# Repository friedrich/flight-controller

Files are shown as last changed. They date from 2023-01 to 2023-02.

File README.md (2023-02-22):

# Flight controller

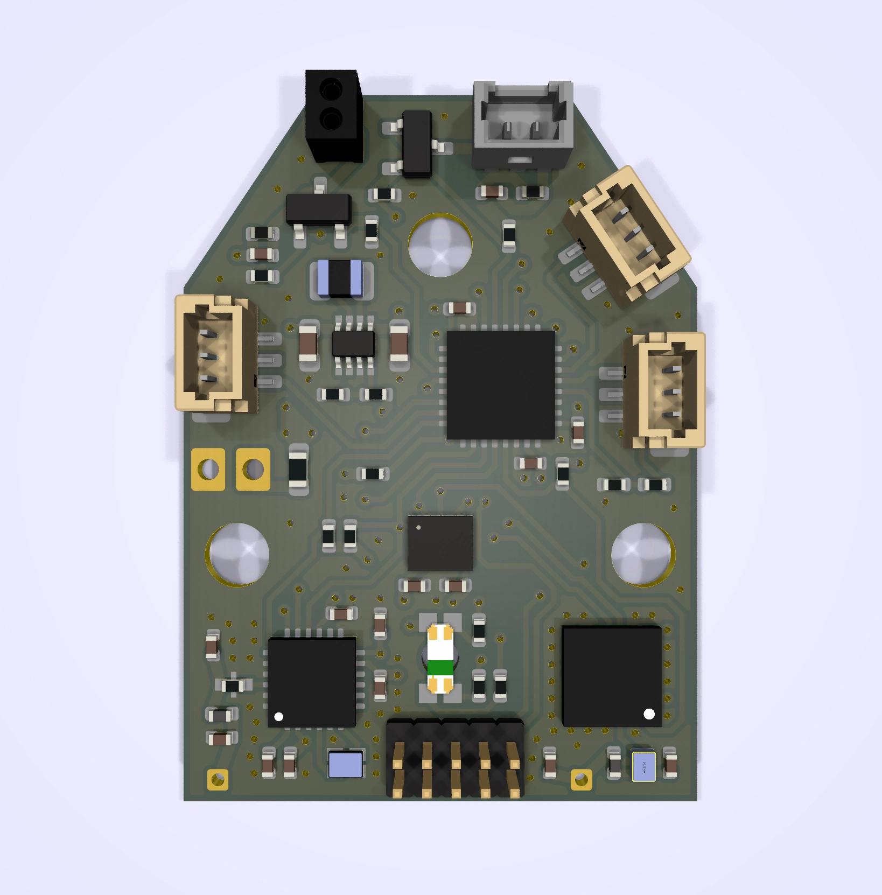
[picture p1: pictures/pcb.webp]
rendering

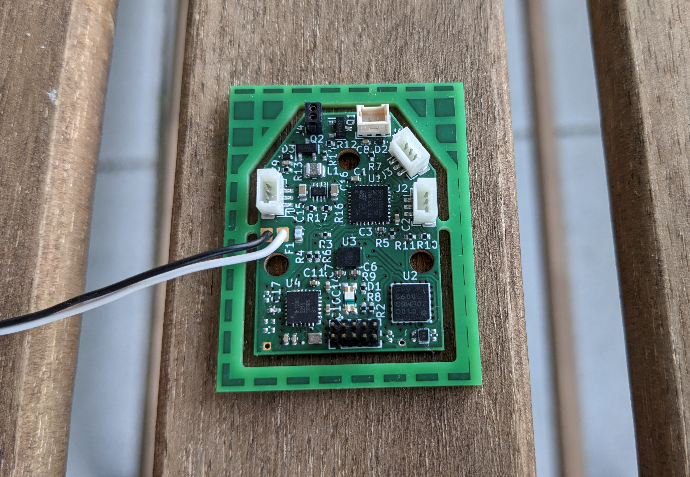
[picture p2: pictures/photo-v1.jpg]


# Hardware features

- :heavy_check_mark: Voltage regulator delivering 3.3 V to the ICs
- :x: Battery voltage monitor
  - Battery voltage monitor pin PA10 is not connected to a DAC.
- :heavy_check_mark: Pulse width modulated power supply of the main and tail rotor motors
- :x: Current monitor of the main and tail rotor motors
  - Pins PF0 and PF1 are not connected to any operational amplifiers. This makes
    current sensing inaccurate, since the shunt voltage is quite low.
- :heavy_check_mark: PWM control of the swashplate servos
- :heavy_check_mark: Programming and debugging interface via SWD and SWO
- :heavy_check_mark: Linear acceleration sensor and gyroscope
- :x: GPS receiver
  - No usable signal from antenna.
  - There is no good return path for the antenna signal.
- :x: Radio module with support for BLE, LoRa, FLRC, GFSK and ranging
  - Untested.
  - There is no good return path for the antenna signal.
- :heavy_check_mark: RGB status indicator LED
- :heavy_check_mark: Overcurrent protection (fuse)

## Possible improvements

- Connect reset pins of other ICs to the microcontroller.
- Connect the SX1280 busy pin and multi-purpose digital I/O pins to the
  microcontroller.
- Connect one PIO pin of the GNSS receiver to the microcontroller for TX ready
  notification.
- Add test points to GND, CS, SDI, SDO, SCK, RESET.
- Print version number on the PCB.
- Remove silk screen labels of small compenents.
- Make it possible to manually pull up the BOOT0 pin in case the firmware
  disrupts SWD communication.
- The top internal layer should be a ground plane to ensure a nice return path
  for the RF signal. Make a six layer board with layers: signal, ground, signal,
  power, signal, ground.

# GPIO pins

| Pin  | Function | Configuration |
|---|---|---|
| PA0  | | |
| PA1  | TAIL_CTL | TIM15_CH1N |
| PA2  | LEFT_CTL | TIM2_CH3 |
| PA3  | /RADIO_CS  | output |
| PA4  | /ACCEL_CS  | output |
| PA5  | SCK | SPI1_SCK |
| PA6  | SDI | SPI1_MISO |
| PA7  | SDO | SPI1_MOSI |
| PA8  | | |
| PA9  | | |
| PA10 | BATT_MON | |
| PA11 | RIGHT_CTL  | TIM4_CH1 |
| PA12 | BACK_CTL | TIM4_CH2 |
| PA13 | SWDIO | SWDIO |
| PA14 | SWCLK | SWCLK |
| PA15 | | |
| PB0  | /GNSS_CS | output |
| PB3  | SWO | TRACESWO |
| PB4  | LED_R | TIM3_CH1 |
| PB5  | LED_G | TIM3_CH2 |
| PB6  | MAIN_CTL | TIM16_CH1N |
| PB7  | LED_B | TIM3_CH4 |
| PF0  | MAIN_SENSE | ADC1_IN10 |
| PF1  | TAIL_SENSE | ADC2_IN10 |

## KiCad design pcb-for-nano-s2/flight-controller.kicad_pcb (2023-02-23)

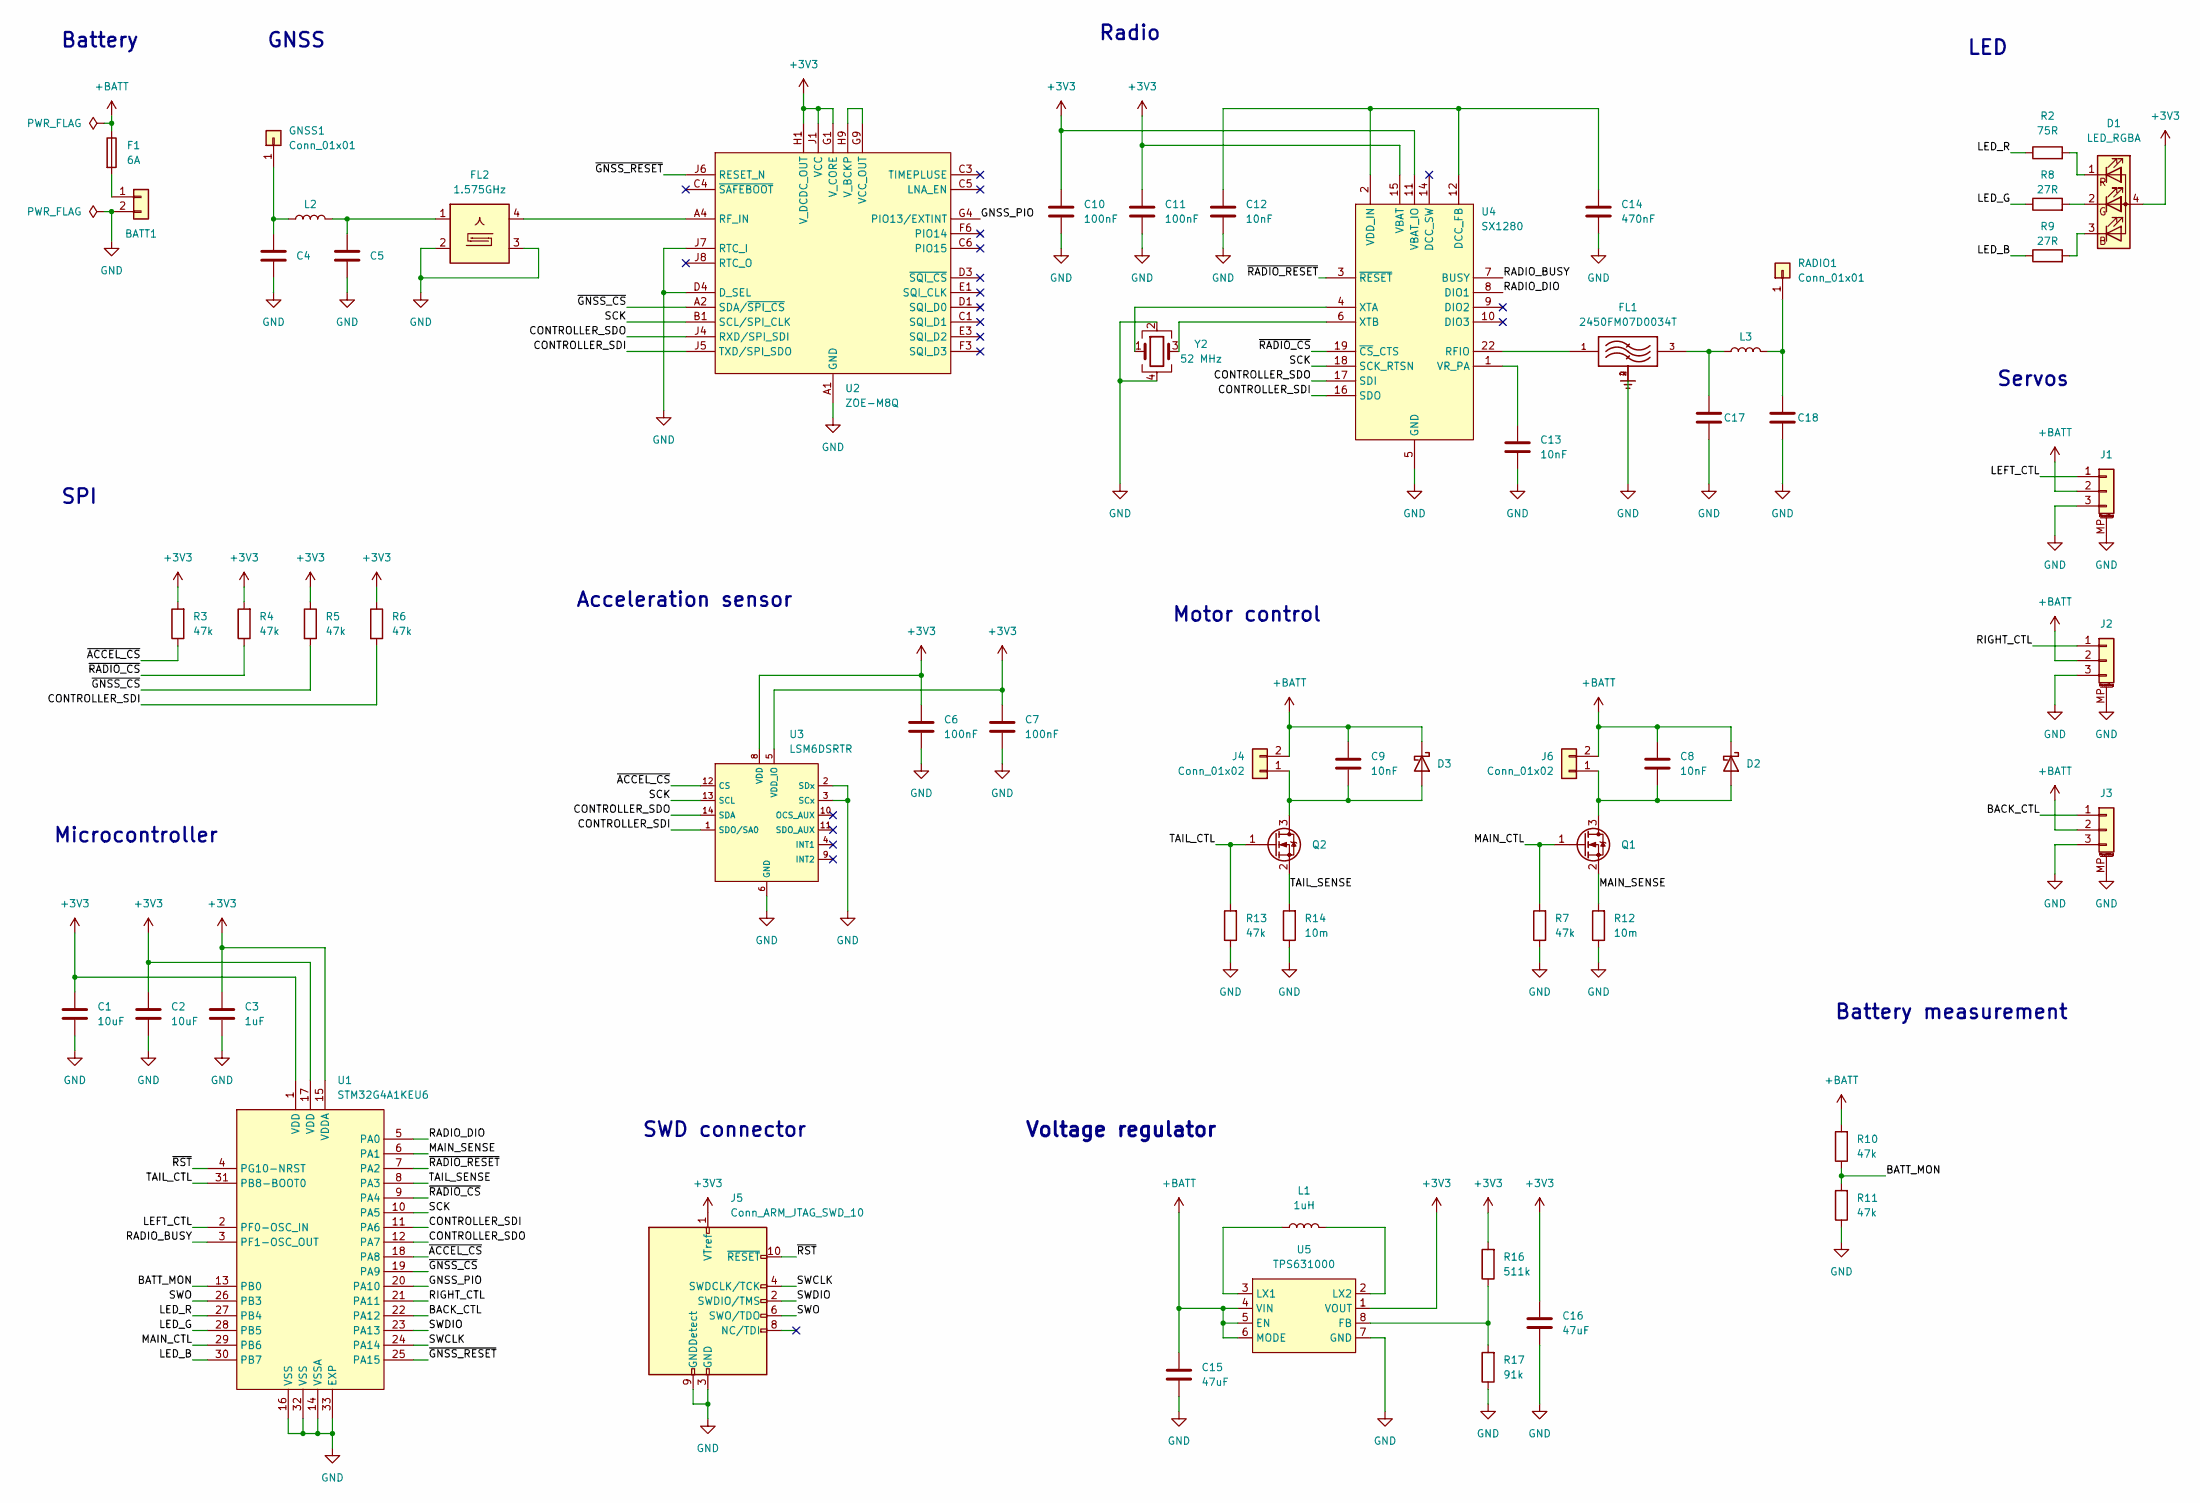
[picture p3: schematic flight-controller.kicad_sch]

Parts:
BATT1: Conn_01x02; Conn
C1, C2: 10uF; C_0402_1005Metric; MPN GRM155R60J106ME15D
C3: 1uF; C_0402_1005Metric; MPN CL05A105MQ5NNNC
C4, C5, C17, C18: C_0402_1005Metric
C6, C7, C10, C11: 100nF; C_0402_1005Metric; MPN CL05A104KA5NNNC
C8, C9, C12, C13: 10nF; C_0402_1005Metric; MPN CL05B103KB5NNNC
C14: 470nF; C_0402_1005Metric; MPN CL05A474KP5NNNC
C15, C16: 47uF; C_0603_1608Metric; MPN GRM188R60J476ME15D
D1: LED_RGBA; LED_156125M173000; MPN 156125M173000
D2, D3: D_Schottky; D_0402_1005Metric; MPN RB521S-30L2-TP
F1: 6A; Fuse_0603_1608Metric; MPN 0686F6000-01
FL1: 2450FM07D0034T; FIL_2450FM07D0034T; MPN 2450FM07D0034T
FL2: 1.575GHz; Filter_1411-5_1.4x1.1mm; MPN AFS14A04-1575.42-T3
GNSS1: Conn_01x01; Antenna
J1, J2, J3: BM03B-SRSS-TBLFSN; JST_SH_BM03B-SRSS-TB_1x03-1MP_P1.00mm_Vertical; MPN CI1103M1VR0-NH
J4: Conn_01x02; PinHeader_1x02_P1.27mm_Vertical; MPN 851-87-002-10-001101
J5: Conn_ARM_JTAG_SWD_10; PinHeader_2x05_P1.27mm_Vertical; MPN GRPB052VWVN-RC
J6: Conn_01x02; Molex_PicoBlade_53047-0210_1x02_P1.25mm_Vertical; MPN 0530470210
L1: 1uH; 0806; MPN DFE201612E-1R0M=P2
L2, L3: L_0402_1005Metric
Q1, Q2: Q_NMOS_GSD; SOT-23; MPN IRLML6244TRPBF
R2: 75R; R_0402_1005Metric; MPN RC0402JR-0775RL
R3, R4, R5, R6, R7, R10, R11, R13: 47k; R_0402_1005Metric; MPN RC0402JR-0747KL
R8, R9: 27R; R_0402_1005Metric; MPN RC0402JR-0727RL
R12, R14: 10m; R_0402_1005Metric; MPN ERJ-2LWFR010X
R16: 511k; R_0402_1005Metric; MPN RC0402FR-07511KL
R17: 91k; R_0402_1005Metric; MPN RC0402FR-0791KL
RADIO1: Conn_01x01; Antenna
U1: STM32G4A1KEU6; UFQFPN-32-1EP_5x5mm_P0.5mm_EP3.5x3.5mm; MPN STM32G4A1KEU6
U2: ZOE-M8Q; componentsearchengine-BGA51C50P9X9_450X450X110; MPN ZOE-M8Q-0
U3: LSM6DSRTR; LGA-14_3x2.5mm; MPN LSM6DSRTR
U4: SX1280; HVQFN-24-1EP_4x4mm_P0.5mm_EP2.6x2.6mm; MPN SX1280IMLTRT
U5: TPS631000; SC-70-8; MPN TPS631000DRLR
Y2: 52 MHz; XTAL_ECS-520-8-47-CKM-TR; MPN ECS-520-8-47-CKM-TR

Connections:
+3V3: C1.1, C2.1, C3.1, C6.1, C7.1, C10.1, C11.1, C16.1, D1.4 (A), J5.1 (VTref), R3.2, R4.2, R5.1, R6.1, R16.2, U1.1 (VDD), U1.15 (VDDA), U1.17 (VDD), U2.G1 (V_CORE), U2.H1 (V_DCDC_OUT), U2.J1 (VCC), U2.J2 (VCC), U3.5 (VDD_IO), U3.8 (VDD), U4.11 (VBAT_IO), U4.15 (VBAT), U5.1 (VOUT)
+BATT: C8.1, C9.1, C15.1, D2.1 (K), D3.1 (K), F1.1, J1.2, J2.2, J3.2, J4.2, J6.2, R10.2, U5.4 (VIN), U5.5 (EN), U5.6 (MODE)
/BACK_CTL: J3.1, U1.22 (PA12)
/BATT_MON: R10.1, R11.2, U1.13 (PB0)
/CONTROLLER_SDI: R6.2, U1.11 (PA6), U2.J5 (TXD/SPI_SDO), U3.1 (SDO/SA0), U4.16 (SDO)
/CONTROLLER_SDO: U1.12 (PA7), U2.J4 (RXD/SPI_SDI), U3.14 (SDA), U4.17 (SDI)
/GNSS_PIO: U1.20 (PA10), U2.G4 (PIO13/EXTINT)
/LED_B: R9.1, U1.30 (PB7)
/LED_G: R8.1, U1.28 (PB5)
/LED_R: R2.1, U1.27 (PB4)
/LEFT_CTL: J1.1, U1.2 (PF0-OSC_IN)
/MAIN_CTL: Q1.1 (G), R7.2, U1.29 (PB6)
/MAIN_SENSE: Q1.2 (S), R12.2, U1.6 (PA1)
/RADIO_BUSY: U1.3 (PF1-OSC_OUT), U4.7 (BUSY)
/RADIO_DIO: U1.5 (PA0), U4.8 (DIO1)
/RIGHT_CTL: J2.1, U1.21 (PA11)
/SCK: U1.10 (PA5), U2.B1 (SCL/SPI_CLK), U3.13 (SCL), U4.18 (SCK_RTSN)
/SWCLK: J5.4 (SWDCLK/TCK), U1.24 (PA14)
/SWDIO: J5.2 (SWDIO/TMS), U1.23 (PA13)
/SWO: J5.6 (SWO/TDO), U1.26 (PB3)
/TAIL_CTL: Q2.1 (G), R13.2, U1.31 (PB8-BOOT0)
/TAIL_SENSE: Q2.2 (S), R14.2, U1.8 (PA3)
/~ACCEL_CS: R3.1, U1.18 (PA8), U3.12 (CS)
/~GNSS_CS: R5.2, U1.19 (PA9), U2.A2 (SDA/~SPI_CS)
/~GNSS_RESET: U1.25 (PA15), U2.J6 (RESET_N)
/~RADIO_CS: R4.1, U1.9 (PA4), U4.19 (~CS_CTS)
/~RADIO_RESET: U1.7 (PA2), U4.3 (~RESET)
/~RST: J5.10 (~RESET), U1.4 (PG10-NRST)
GND: BATT1.2, C1.2, C2.2, C3.2, C4.1, C5.1, C6.2, C7.2, C10.2, C11.2, C12.2, C13.2, C14.2, C15.2, C16.2, C17.1, C18.1, FL1.2, FL1.4, FL2.2, FL2.3, FL2.5, J1.3, J1.MP (MountPin), J2.3, J2.MP (MountPin), J3.3, J3.MP (MountPin), J5.3 (GND), J5.5 (GND), J5.9 (GNDDetect), R7.1, R11.1, R12.1, R13.1, R14.1, R17.1, U1.14 (VSSA), U1.16 (VSS), U1.32 (VSS), U1.33 (EXP), U2.A1 (GND), U2.A3 (GND), U2.A5 (GND), U2.A7 (GND), U2.A8 (GND), U2.A9 (GND), U2.B9 (GND), U2.C7 (GND), U2.C9 (GND), U2.D4 (D_SEL), U2.D6 (GND), U2.D9 (GND), U2.E7 (GND), U2.F7 (GND), U2.G3 (GND), U2.G6 (GND), U2.G7 (GND), U2.J3 (GND), U2.J7 (RTC_I), U2.J9 (GND), U3.2 (SDx), U3.3 (SCx), U3.6 (GND), U3.7 (GND), U4.5 (GND), U4.13 (GND), U4.20 (GND), U4.21 (GND), U4.23 (GND), U4.24 (GND), U4.25 (GND), U5.7 (GND), Y2.2, Y2.4
unnamed: BATT1.1, F1.2
unnamed: C5.2, FL2.1, L2.2
unnamed: C17.2, FL1.3, L3.1
unnamed: D1.3 (BK), R9.2
unnamed: D1.2 (GK), R8.2
unnamed: D1.1 (RK), R2.2
unnamed: C8.2, D2.2 (A), J6.1, Q1.3 (D)
unnamed: C9.2, D3.2 (A), J4.1, Q2.3 (D)
unnamed: C4.2, GNSS1.1, L2.1
unnamed: C18.2, L3.2, RADIO1.1
unnamed: FL2.4, U2.A4 (RF_IN)
unnamed: U2.G9 (VCC_OUT), U2.H9 (V_BCKP)
unnamed: C12.1, C14.1, U4.2 (VDD_IN), U4.12 (DCC_FB)
unnamed: FL1.1, U4.22 (RFIO)
unnamed: C13.1, U4.1 (VR_PA)
unnamed: U4.4 (XTA), Y2.1
unnamed: U4.6 (XTB), Y2.3
unnamed: R16.1, R17.2, U5.8 (FB)
unnamed: L1.1, U5.3 (LX1)
unnamed: L1.2, U5.2 (LX2)

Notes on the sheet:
Acceleration sensor
Microcontroller
Battery
GNSS
SWD connector
Battery measurement
Radio
SPI
Voltage regulator
Motor control
LED
Servos

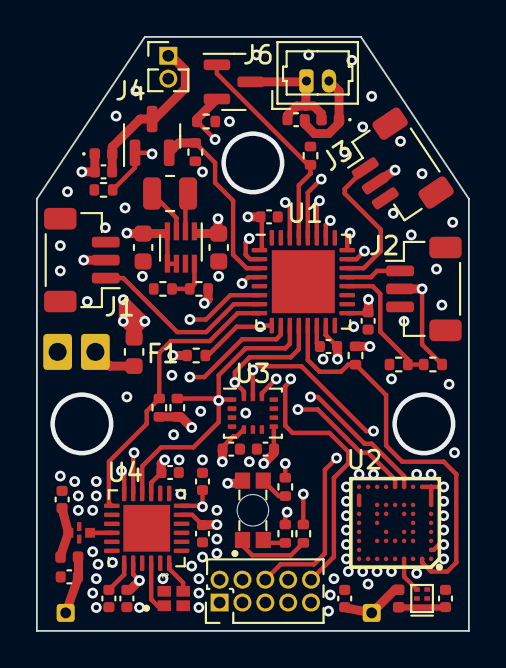
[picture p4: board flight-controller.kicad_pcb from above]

Board: 6 copper layers, 24.0 x 33.0 mm, 59 parts (0 on the bottom side), 49 nets.

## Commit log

2023-01-18 add PCB
    [flight-controller.kicad_pcb, flight-controller.kicad_sch]
2023-01-18 add impedance matching circuits for antennas
    [flight-controller.kicad_pcb, flight-controller.kicad_sch]
2023-01-18 fix component infos
    [flight-controller.kicad_pcb, flight-controller.kicad_sch]
2023-01-18 remove solder mask expansion
    [flight-controller.kicad_pcb]
2023-02-20 update Kicad file version
    [flight-controller.kicad_pcb, flight-controller.kicad_sch]
2023-02-20 unfill zones
    [flight-controller.kicad_pcb]
2023-02-22 update PCB from schematic
    [flight-controller.kicad_pcb]
2023-02-22 remove small components' labels
    [flight-controller.kicad_pcb]
2023-02-22 change PCB design to six layers
    [flight-controller.kicad_pcb]
2023-02-23 fix connections and add new ones in schematic
    [flight-controller.kicad_pcb, flight-controller.kicad_sch]
